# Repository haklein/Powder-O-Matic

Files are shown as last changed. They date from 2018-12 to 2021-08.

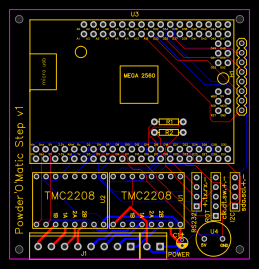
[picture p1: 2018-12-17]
schematics/PCB_Powder-O-Matic-Stepper-TMC2208-V1_20181217092319.png

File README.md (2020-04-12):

Powder'O'Matic Step Readme
==========================

## Overview

This Sketch controls two stepper motors via two TCM2208 stepper drivers. The drivers 
are controlled via dir/step pins and configured via Serial 2 and 3. Serial 1 is being
used to fetch values from a the scale. The target value is adjusted with a KY-040
rotary encoder. Dispensing can be started by pressing the push button of the rotary
encoder. A SSD1306 OLED display is used to display the current state, actual and target
value. The Kern scale needs to be configured for command mode ("rE Cr") with 19200 baud. 
The default values are set up for grain.
  
The KY-040 is evaluated by attaching a pin interrupt to the CLK signal (rotaryIsr())
The Stepper A is being turned via UART commands. Stepper B uses the AccelStep library.

Operation can be seen here: https://youtu.be/FhTphJCxM40 (prototype with a KERN PCB100-3)
and here: https://youtu.be/DZrE01YJ6Ys (final version in nice case with A&D FX120i balance)

The Autotrickler hardware (trickler and stepper motor adapter for the Lee Powder Thrower)
can be bought here: https://www.autotrickler.com

While Adam's Autotrickler hardware is the preferred option, you can find a motor adapter 
for the RCBS Powder Trickler #2 in the designs folder. A pulley for the RCBS pipe and a
case for the provided PCB layout can also be seen there. The case is ready-to-use for the
PCB, an SSD1309 1,54" OLED Display, the rotary, two subminiature switches (power and auto
mode), a DC socket and two G36 4-pin sockets for the stepper motors.

A complete BOM can be found here: https://github.com/haklein/Powder-O-Matic/blob/master/BOM.md

As I've been aksed multiple times, these config settings for the FX120i do work fine for me:

 btPr 2, bPs 5, Prt 3, Spd 20, trc 0, cond 0.

## Requirements

### Arduino libraries

- ArduinoMenu library
- TimerOne
- ClickEncoder - https://github.com/0xPIT/encoder
- Adafruit GFX Library
- TMC2208Stepper
- AccelStepper
- Adafruit SSD1306

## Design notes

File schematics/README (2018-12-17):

EasyEDA source (JSON file), PDF schematics, gerber file and PCB PNG.

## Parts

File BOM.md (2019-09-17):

Bill of Material
================

- P'o'M PCB (see schematics folder) or breadboard/prototype PCB
- RobotDyn Mega 2560 PRO (Embed) fitting the P'o'M PCB (or any other Mega 2560 based arduino if you do your own PCB)
- TMC2208 Board (I'm using the 1.0 from fysetc.com, make sure it's one where you can solder-bridge the NC pin to the
  serial input of the TMC (as that's used on the P'o'M PCB). You need one board for the trickler and one for the thrower.
- piezzo buzzer (U4) - I'm using a KEPO KPT-G1420A-K8437. It's a bit too big for the PCB but still connectable with a bit
  of tweaking
- capacitor (220 µF)
- resistors (R1 + R2) - 1k
- screw terminalls - Watch the spacing of the PCB, I'm using DECA MA212-350M02 
- pin headers and sockets
- RS232 ttl level converter, watch out, some of the ebay PCBs run insanely hot and don't work reliable (mostly SMD ones 
  without LED). The ones with MAX232 in DIP and LEDs worked fine for me
- KY040 rotary encoder
- SSD1306 display (resp. SSD1309 with 1.5" if you want to use the 3d printed case from the designs folder)
- two miniature switches for power switch and automatic mode switch
- DC socket
- GX16-4 plug and socket for the steppers
- 3d printed case from the designs folder (perfect fit for the P'o'M PCB)

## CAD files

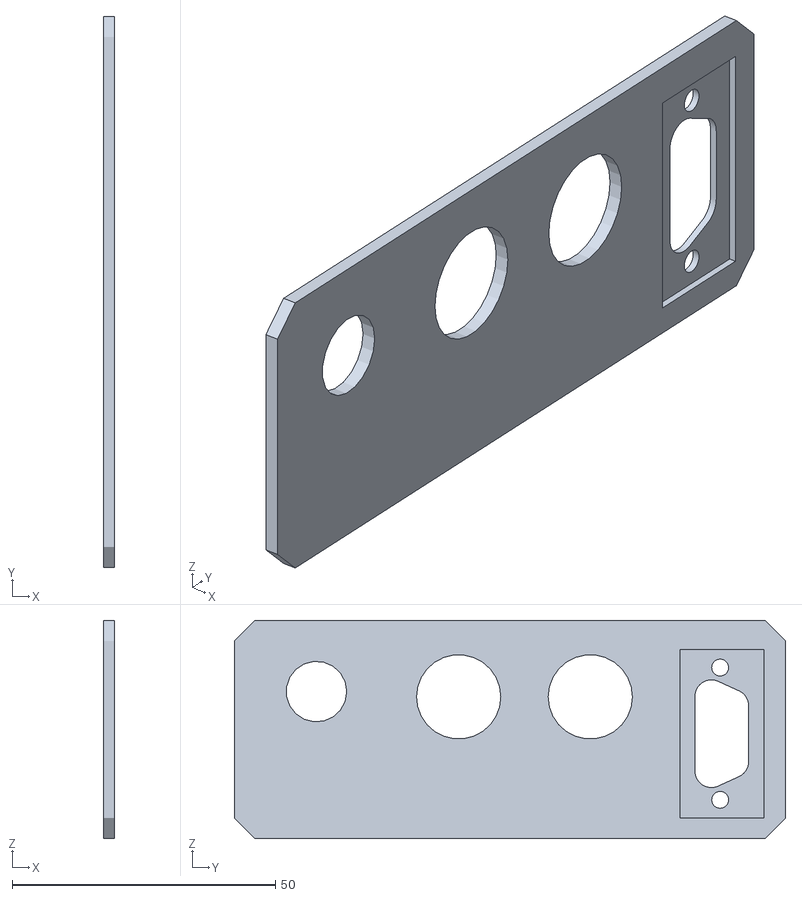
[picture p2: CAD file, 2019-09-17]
designs/pom_back_panel.stl
2.00 x 104.7 x 41.4

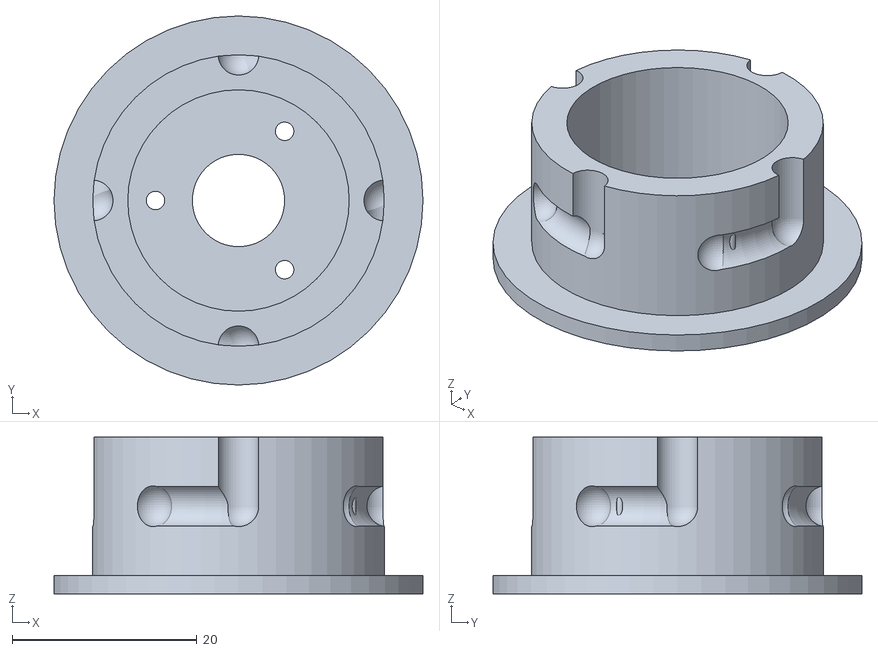
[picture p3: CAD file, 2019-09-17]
designs/straw-replacement_bottom.stl
40.0 x 40.0 x 17.0

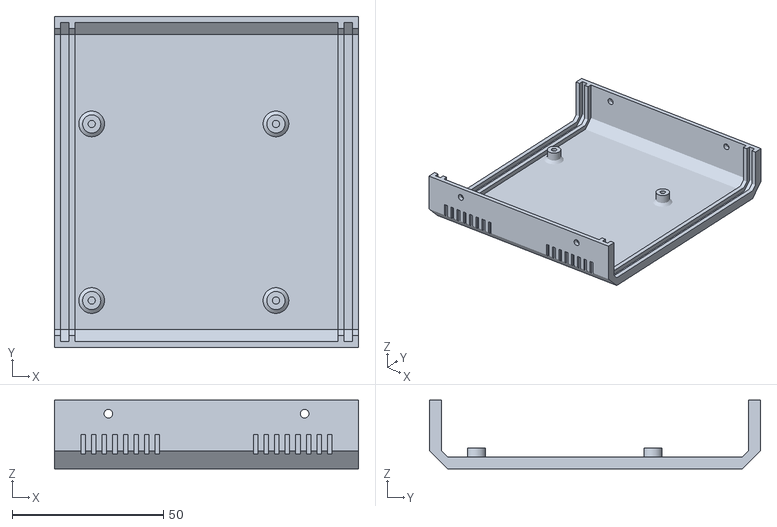
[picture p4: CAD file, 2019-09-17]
designs/pom_case_bottom.stl
100.6 x 109.5 x 22.8

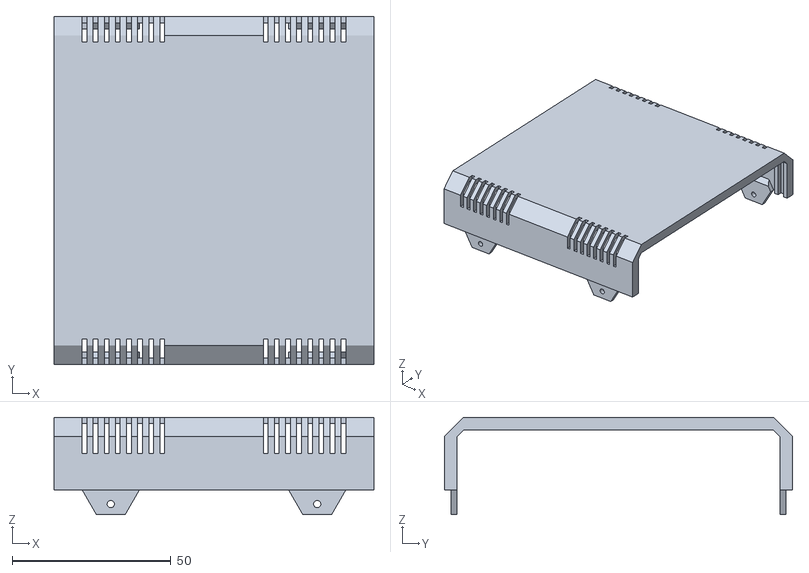
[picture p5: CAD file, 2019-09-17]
designs/pom_case_top.stl
100.6 x 109.5 x 30.6

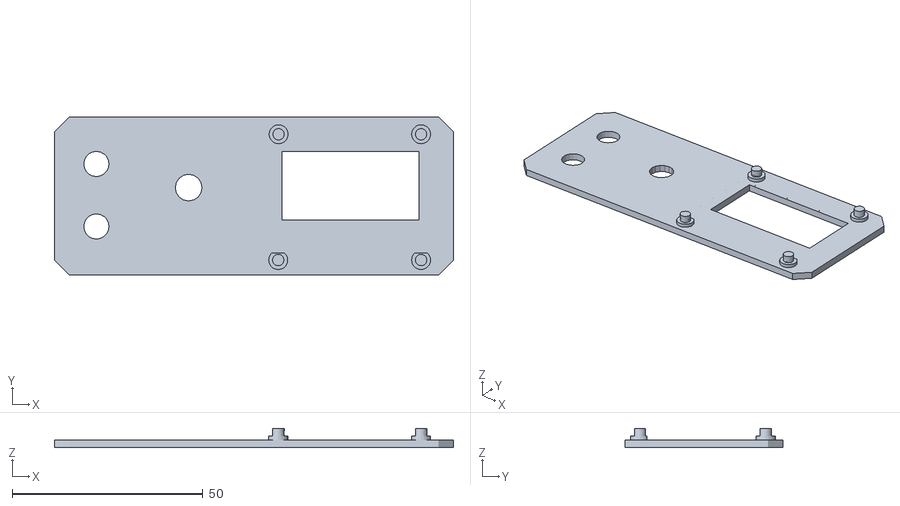
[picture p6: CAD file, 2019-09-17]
designs/pom_front_panel.stl
104.7 x 41.4 x 5.00

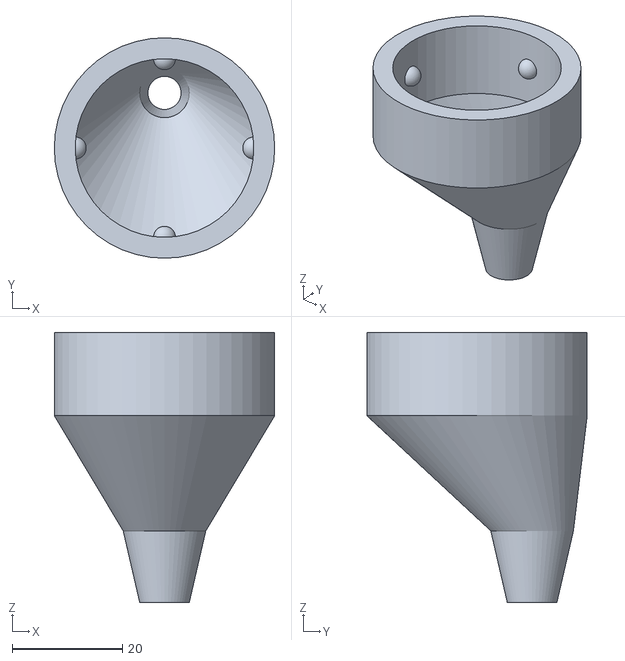
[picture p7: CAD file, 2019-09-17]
designs/straw-replacement_top.stl
40.0 x 40.0 x 49.0

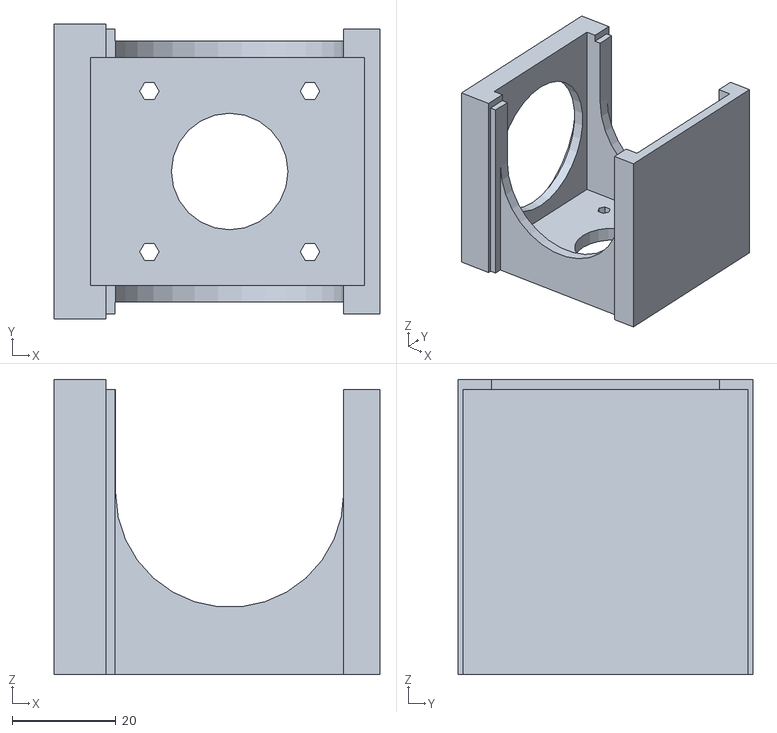
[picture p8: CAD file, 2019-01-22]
designs/RCBS_Trickler_NEMA17_mount.stl
62.9 x 57.0 x 57.0

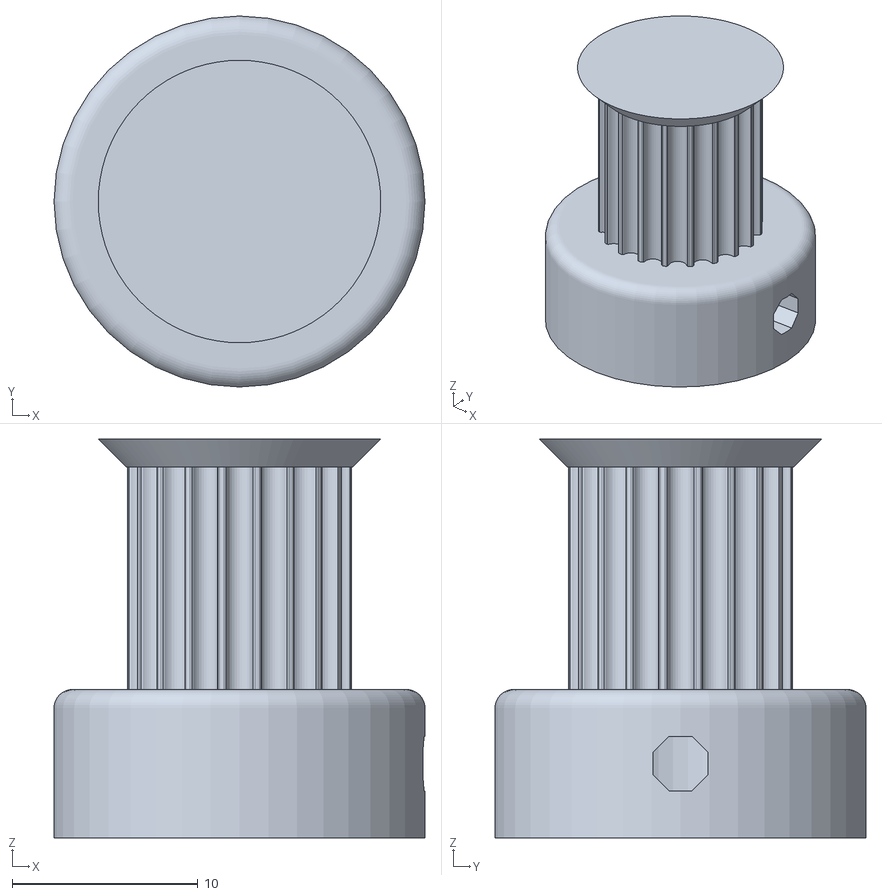
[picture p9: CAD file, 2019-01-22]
designs/RCBS_Trickler_shaft_pulley.stl
20.0 x 20.0 x 21.5

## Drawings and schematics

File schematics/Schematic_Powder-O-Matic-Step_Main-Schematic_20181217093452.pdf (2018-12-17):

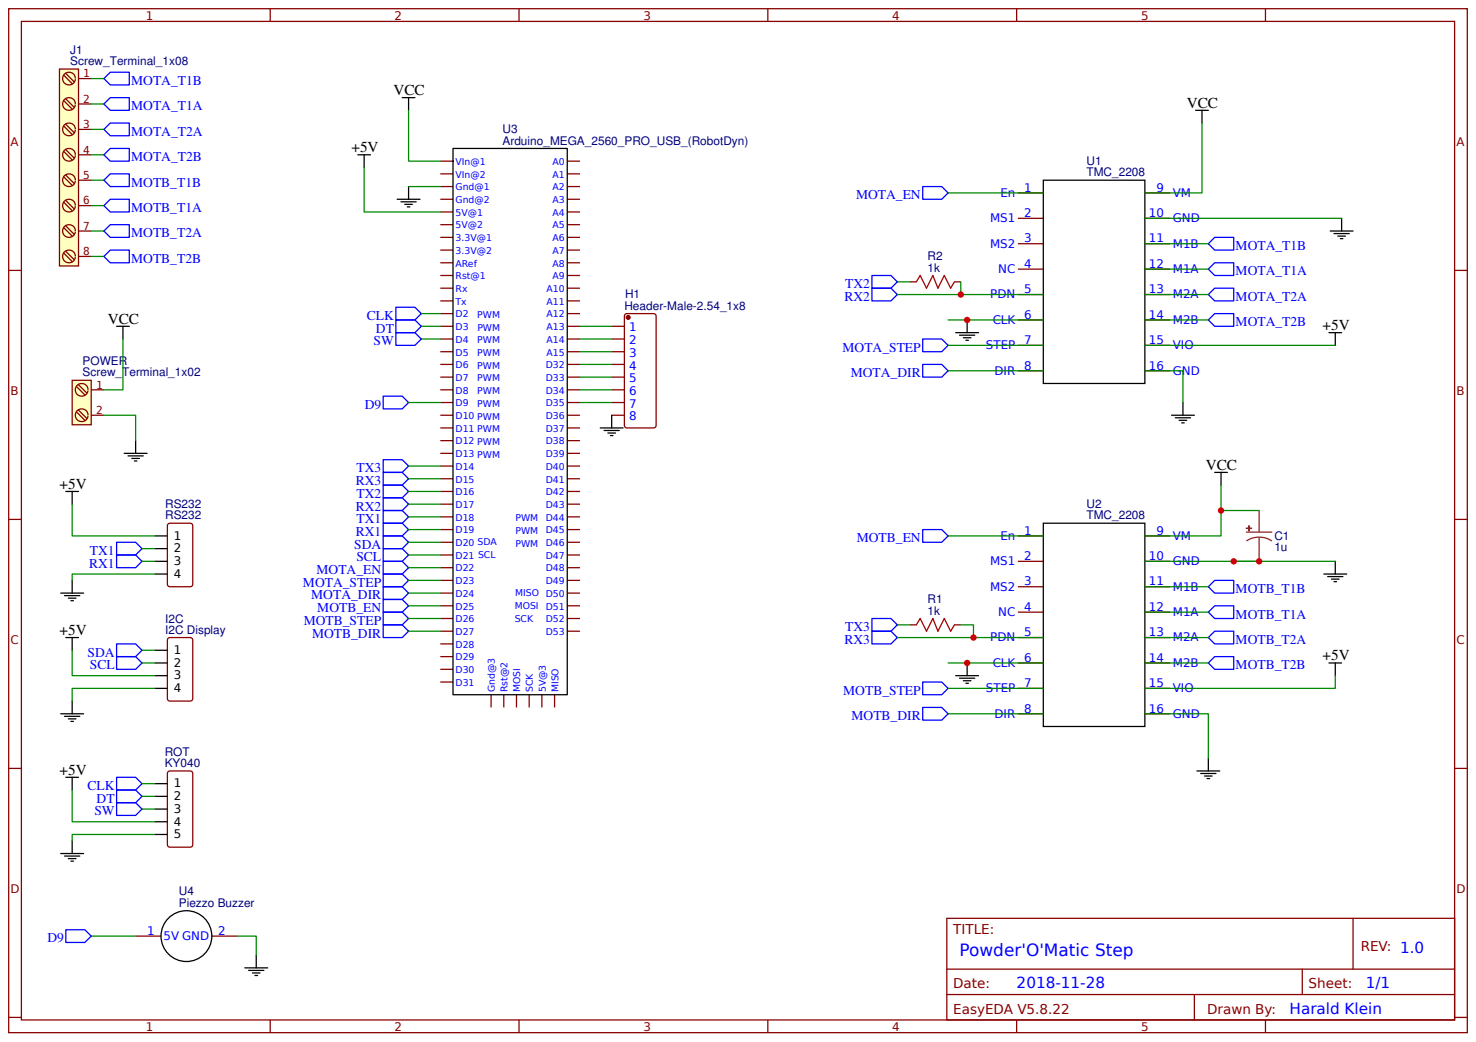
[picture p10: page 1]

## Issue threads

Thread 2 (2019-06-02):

Hilfe

Rajakob, 2019-06-02:
Guten Tag. Ich habe damit begonnen Ihr Projekt umzusetzen. Besten Dank vorweg eine wirklich tolle Lösung.  Ich verwende eine AnD FX120i jedoch scheitert die automatische Tarierung. Könne Sie mir bitte die Einstellungen mitteilen, welche Sie an der Waage gemacht haben damit die Waage von extern Tariert werden kann? Ebenfalls kann Ich nicht wie in Ihrem letzten Video die einzelnen Einstellungen z.B Trickler mA einstellen. Ist der Code noch Ihre „alte“ Version? Besten Dank für Ihre Hife. Freundliche Grüsse aus der Schweiz. Raoul Jakob
J.raoul@hotmail.com

haklein, 2021-08-25:
Die Einstellungen sollten jetzt wieder funktionieren. Die Einstellungen an der Waage kann ich derzeit nicht nachsehen, aber die optionen sind so weit schluessig im Handbuch erklaert.

Closed 2021-08-25.

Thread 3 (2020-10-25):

Display set-up menu

RowanNL, 2020-10-25:
Hello,

I've got the program and trickler working but i have a problem with entering the set-up menu.
When pressing the rotary encoder while start up it will enter set up but the whole screen just turns white.
I just used your program, I've tried both displays but the both do the same.

Can you help me out?

Thx!

I really love the powder-o-matic! It would be really nice to have the set up working as well.

RowanNL, 2020-12-12:
Gütentag, Wenn ich durch Drücken beim Start in das Setup-Menü gehen möchte, bleibt der Bildschirm weiß. Kannst du mir helfen? Es funktioniert auf deinem YouTube-Kanal...

danke im Voraus

RowanNL, 2021-01-13:
Hello Harald,

Could you help us?

regards,

RowanNL, 2021-01-13:
Hello Harald,

can you help us?

regards,

haklein, 2021-08-25:
I've found the reason for this issue with new arduino versions. Will be fixed in a few minutes.

Closed 2021-08-25.

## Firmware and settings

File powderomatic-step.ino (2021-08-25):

/*

     Powder'O'Matic Step

    Copyright (c) 2018 Harald Klein <hari@vt100.at>

    Licensed under GPL Version 3 - https://www.gnu.org/licenses/gpl-3.0.html

    This Sketch controls two stepper motors via two TCM2208 stepper drivers. The drivers
    are controlled via dir/step pins and configured via Serial 2 and 3. Serial 1 is being
    used to fetch values from a Kern PCB scale. The target value is adjusted with a KY-040
    rotary encoder. Dispensing can be started by pressing the push button of the rotary
    encoder. A SSD1306 OLED display is used to display the current state, actual and target
    value. The Kern scale needs to be configured for command mode ("rE Cr") with 19200 baud.
    The default values are set up for grain.

    The KY-040 is evaluated by attaching a pin interrupt to the CLK signal (rotaryIsr())
    The Stepper A is being turned via a timer interrupt (timer 5). Speed is adjusted by the
    microsteps() function of the TMC2208Stepper library.
*/

/*
  // gramm values
  #define MASSFILL_FAST_DELTA 0.05
  #define MASSFILL_SLOW_DELTA 0.02
  #define TRICKLE_DELTA 0.01
*/

// #define BALANCE_TYPE 1 // kern PCB 100-3
// #define BALANCE_TYPE 2 // A&D FX120i
// #define BALANCE_TYPE 3 // Sartorius
#define BALANCE_TYPE 2

// settings for Kern PCB
#if BALANCE_TYPE == 1
// grain values
#define MASSFILL_FAST_DELTA 1.4  // 1.2
#define MASSFILL_SLOW_DELTA 0.3
#define TRICKLE_DELTA 0.06
#define TRICKLE_DELAY 200

// settings for A&D FX120i
#elif BALANCE_TYPE == 2
#define MASSFILL_FAST_DELTA 0.8  // 1.2
#define MASSFILL_SLOW_DELTA 0.12
#define TRICKLE_DELTA 0.04
#define TRICKLE_DELAY 0

#endif


#define MOTA_SPEED_MAX 820 // 210000 / 256
#define MOTA_SPEED_MIN 59 // 15000 / 256

#define AUTOMODE_PIN 35 // set to 0 if no automode switch is connected

#define debug 20

// trickler stepper setup
#define MOTA_DIR 24
#define MOTA_STEP 23
#define MOTA_ENA 22
#define MOTA_MSTEPS 256 // 16
#define MOTA_SERIAL Serial2
#define MOTA_CURRENT_MA 500

// thrower stepper setup
#define MOTB_DIR 27
#define MOTB_STEP 26
#define MOTB_ENA 25
#define MOTB_MSTEPS 2
#define MOTB_SERIAL Serial3
#define MOTB_CURRENT_MA 300

#define THROWER_POSITION 170
#define THROWER_DELAY 300
#define THROWER_ENABLED true

#define BUZZER_PIN 9
#define BUZZER_SUCCESS_FREQ 2000
#define BUZZER_SUCCESS_DURATION 500
#define BUZZER_ERROR_FREQ 4000
#define BUZZER_ERROR_DURATION 300
#define BUZZER_ERROR_DELAY 300
#define BUZZER_ERROR_BEEP_COUNT 5

// baudrates
#define TMC2208_BAUDRATE 460800
#define KERN_PCB_BAUDRATE 19200

#define CONSOLE_BAUDRATE 115200

// mydisplay settings
#define OLED_RESET 34 // -1  Set to -1 for 0,96" SSD1306 display. 1.54" SSD1309 needs reset, pin 34 is recommended
#define SCREEN_WIDTH 128 // OLED display width, in pixels
#define SCREEN_HEIGHT 64 // OLED display height, in pixels
#define OLED_I2C_ADDRESS 0x3D // 0x3c 0.96" 

#define fontX 5
#define fontY 9
#define MAX_DEPTH 3
/// #define textScale 1

// rotary encoder settings
#define K040_SW 4  // D22, pin 74
#define K040_DT 3 // D24, pin 72
#define K040_CLK 2   //  int pin  alt: // D26, pin 70

#define ROTARY_DELTA_VALUE -0.1  // change sign to adjust for rotary direction
#define ROTARY_DEBOUNCE_MILLIS 5

#define CONFIG_MAGIC 0xdeadbeef
#define CONFIG_MIN_VER 1
#define CONFIG_VER 1

// config section end

#include <EEPROM.h>
#include <Arduino.h>  // for type definitions

#include <menu.h>
#include <TimerOne.h>

#include <ClickEncoder.h>
#include <menuIO/clickEncoderIn.h>
#include <menuIO/keyIn.h>
#include <menuIO/chainStream.h>
#include <menuIO/serialOut.h>
#include <menuIO/adafruitGfxOut.h>
#include <menuIO/serialIn.h>

#include <TMC2208Stepper.h>
#include <AccelStepper.h>

#include <SPI.h>
#include <Wire.h>
#include <Adafruit_GFX.h>
#include <Adafruit_SSD1306.h>

template <class T> int EEPROM_writeAnything(int ee, const T& value)
{
  const byte* p = (const byte*)(const void*)&value;
  unsigned int i;
  for (i = 0; i < sizeof(value); i++)
    EEPROM.write(ee++, *p++);
  return i;
}

template <class T> int EEPROM_readAnything(int ee, T& value)
{
  byte* p = (byte*)(void*)&value;
  unsigned int i;
  for (i = 0; i < sizeof(value); i++)
    *p++ = EEPROM.read(ee++);
  return i;
}

struct config_t {
  long int magic = CONFIG_MAGIC;
  int confVer = CONFIG_VER;
  int balanceType = BALANCE_TYPE;
  int motaCurrent = MOTA_CURRENT_MA;
  int motaSpeedMax = MOTA_SPEED_MAX;
  int motaSpeedMin = MOTA_SPEED_MIN;
  int motaMsteps = MOTA_MSTEPS;
  int motbCurrent = MOTB_CURRENT_MA;
  int motbMsteps = MOTB_MSTEPS;
  bool throwerEnabled = THROWER_ENABLED;
  int throwerDelay = THROWER_DELAY;
  int throwerPosition = THROWER_POSITION;
  float massfillFastDelta = MASSFILL_FAST_DELTA;
  float massfillSlowDelta = MASSFILL_SLOW_DELTA;
  float trickleDelta = TRICKLE_DELTA;
  int trickleDelay = TRICKLE_DELAY;
} configData;

ClickEncoder clickEncoder(K040_CLK, K040_DT, K040_SW, 4); // last parameter: steps per notch
ClickEncoderStream encStream(clickEncoder, 1);

TMC2208Stepper driverA = TMC2208Stepper(&MOTA_SERIAL);
TMC2208Stepper driverB = TMC2208Stepper(&MOTB_SERIAL);

AccelStepper stepperB(AccelStepper::DRIVER, MOTB_STEP, MOTB_DIR);

Adafruit_SSD1306 myDisplay(SCREEN_WIDTH, SCREEN_HEIGHT, &Wire, OLED_RESET);

volatile float targetValue = 5;
bool automaticModeEnabled = false; //AUTOMODE_PIN != 0 ? true : false;

void rotaryISR() {
  static unsigned long lastInterruptTime = 0;
  unsigned long interruptTime = millis();
  unsigned long delta = millis() - lastInterruptTime;
  int multi = sq(500 - min(delta, 500)) / 25000 + 1;

  // debounce 5ms
  if (delta > ROTARY_DEBOUNCE_MILLIS) {

    if (digitalRead(K040_DT) == LOW)
    {
      targetValue = targetValue - ROTARY_DELTA_VALUE * multi;
    }
    else {

      targetValue = targetValue + ROTARY_DELTA_VALUE * multi;
    }
    lastInterruptTime = interruptTime;
  }
}

void timerIsr() {
  clickEncoder.service();
}


const colorDef<uint16_t> colors[6] MEMMODE = {
  {{BLACK, WHITE}, {BLACK, WHITE, WHITE}}, //bgColor
  {{WHITE, BLACK}, {WHITE, BLACK, BLACK}}, //fgColor
  {{WHITE, BLACK}, {WHITE, BLACK, BLACK}}, //valColor
  {{WHITE, BLACK}, {WHITE, BLACK, BLACK}}, //unitColor
  {{WHITE, BLACK}, {BLACK, BLACK, BLACK}}, //cursorColor
  {{BLACK, WHITE}, {WHITE, BLACK, BLACK}}, //titleColor
};

/*
  const colorDef<uint16_t> colors[] MEMMODE = {
  {{WHITE, BLACK}, {WHITE, BLACK, BLACK}}, //bgColor
  {{BLACK, WHITE}, {BLACK, WHITE, WHITE}}, //fgColor
  {{BLACK, WHITE}, {BLACK, WHITE, WHITE}}, //valColor
  {{BLACK, WHITE}, {BLACK, WHITE, WHITE}}, //unitColor
  {{BLACK, WHITE}, {WHITE, WHITE, WHITE}}, //cursorColor
  {{BLACK, WHITE}, {WHITE, BLACK, BLACK}}, //titleColor
  };
*/

result showEvent(eventMask e, navNode& nav, prompt& item) {
  Serial.print(F("event:"));
  Serial.print(e);
  return proceed;
}

result alert(menuOut& o, idleEvent e);
result doAlert(eventMask e, prompt &item);

CHOOSE(configData.balanceType, scaleMenu, "Scale", doNothing, noEvent, noStyle
       , VALUE("Kern PCB 100-3", 1, doNothing, noEvent)
       , VALUE("A&D FX120i", 2, doNothing, noEvent)
       , VALUE("Sartorius", 3, doNothing, noEvent)
      );

SELECT(configData.motaMsteps, motamstepMenu, "Trickler MSteps", doNothing, noEvent, noStyle
       , VALUE("1", 1, doNothing, noEvent)
       , VALUE("2", 2, doNothing, noEvent)
       , VALUE("4", 4, doNothing, noEvent)
       , VALUE("8", 8, doNothing, noEvent)
       , VALUE("16", 16, doNothing, noEvent)
       , VALUE("32", 32, doNothing, noEvent)
       , VALUE("64", 64, doNothing, noEvent)
       , VALUE("128", 128, doNothing, noEvent)
       , VALUE("256", 256, doNothing, noEvent)
      );

SELECT(configData.motbMsteps, motbmstepMenu, "Thrower MSteps", doNothing, noEvent, noStyle
       , VALUE("1", 1, doNothing, noEvent)
       , VALUE("2", 2, doNothing, noEvent)
       , VALUE("4", 4, doNothing, noEvent)
       , VALUE("8", 8, doNothing, noEvent)
       , VALUE("16", 16, doNothing, noEvent)
       , VALUE("32", 32, doNothing, noEvent)
       , VALUE("64", 64, doNothing, noEvent)
       , VALUE("128", 128, doNothing, noEvent)
       , VALUE("256", 256, doNothing, noEvent)
      );

SELECT(configData.throwerEnabled, throwenaMenu, "Thr. Enabled", doNothing, noEvent, noStyle
       , VALUE("Yes", true, doNothing, noEvent)
       , VALUE("No", false, doNothing, noEvent)
      );

MENU(mainMenu, "Powder'O'Matic Setup", doNothing, noEvent, wrapStyle
     , SUBMENU(scaleMenu)
     //     , FIELD(test, "Test", "%", 0, 100, 10, 1, doNothing, noEvent, wrapStyle)
     , FIELD(configData.motaCurrent, "Trickler Cur", "mA", 100, 2000, 100, 10, doNothing, noEvent, noStyle)
     , SUBMENU(motamstepMenu)
     , FIELD(configData.motaSpeedMin, "Tr MinSpd", "", 10, 300, 10, 1, doNothing, noEvent, noStyle)
     , FIELD(configData.motaSpeedMax, "Tr MaxSpd", "", 100, 1500, 100, 10, doNothing, noEvent, noStyle)
     , SUBMENU(throwenaMenu)
     , FIELD(configData.motbCurrent, "Thrower Curr", "mA", 100, 2000, 100, 10, doNothing, noEvent, noStyle)
     , SUBMENU(motbmstepMenu)
     , FIELD(configData.throwerDelay, "Thrower Delay", "ms", 0, 1000, 100, 10, doNothing, noEvent, noStyle)
     , FIELD(configData.throwerPosition, "Thrower Pos", "step", 0, 1000, 100, 10, doNothing, noEvent, noStyle)
     , FIELD(configData.massfillFastDelta, "Fast Delta", "gr", 0.0, 5, 1, 0.1, doNothing, noEvent, noStyle)
     , FIELD(configData.massfillSlowDelta, "Slow Delta", "gr", 0.0, 2, 0.1, 0.01, doNothing, noEvent, noStyle)
     , FIELD(configData.trickleDelta, "Trickle Delta", "gr", 0.0, 0.2, 0.1, 0.01, doNothing, noEvent, noStyle)
     , FIELD(configData.trickleDelay, "Trickle Delay", "ms", 0, 1000, 100, 10, doNothing, noEvent, noStyle)
     , OP("<Save", writeEprom, enterEvent)
     , OP("<Factory defaults", resetEprom, enterEvent)
     //     , EXIT("<Back")
    );


MENU_INPUTS(in, &encStream);

MENU_OUTPUTS(out, MAX_DEPTH
             , ADAGFX_OUT(myDisplay, colors, fontX, fontY, {0, 0, SCREEN_WIDTH / fontX, SCREEN_HEIGHT / fontY})
             , NONE // needs to have two items
            );

NAVROOT(nav, mainMenu, MAX_DEPTH, in, out);

bool writeEprom() {
  Serial.println("Writing EEPROM Config data");
  EEPROM_writeAnything(0, configData);
  return true;
}

bool resetEprom() {
  config_t factoryConfigData;
  EEPROM_writeAnything(0, factoryConfigData);
  return true;
}

void configMenu() {


  myDisplay.clearDisplay();
  myDisplay.setTextSize(1);
  myDisplay.setCursor(0, 0);
  myDisplay.setTextColor(BLACK, WHITE); // 'inverted' text
  myDisplay.println("Powder'O'Matic Stp v1");
  myDisplay.setCursor(0, 14);
  myDisplay.setTextColor(WHITE);
  myDisplay.setTextSize(2);
  myDisplay.println("Setup..");

  myDisplay.display();
  myDisplay.setTextSize(1);

  while (digitalRead(K040_SW) == LOW); // wait until button is released to not feed input into nav.doInput()
  // delay(2000);

  while (true) {

    nav.doInput();
    if (nav.changed(0)) {//only draw if changed
      nav.doOutput();
      myDisplay.display();
    }
  }
}
void setup() {
  Serial.begin(CONSOLE_BAUDRATE);
  Serial1.begin(KERN_PCB_BAUDRATE);
  Serial2.begin(TMC2208_BAUDRATE);
  Serial3.begin(TMC2208_BAUDRATE);

  Serial.println("reading EEPROM config data");
  EEPROM_readAnything(0, configData);
  if ((configData.magic != CONFIG_MAGIC) || (configData.confVer < CONFIG_MIN_VER)) {
    Serial.println("ERROR, invalid EEPROM config data, writing default config");
    config_t newConfigData;
    EEPROM_writeAnything(0, newConfigData);
    configData = newConfigData;
    Serial.print("initialized EEPROM config data to default values, version: ");
    Serial.println(configData.confVer);
    delay(100);

  } else {
    Serial.print("EEPROM config valid, version: ");
    Serial.println(configData.confVer);
  }


  Serial.println("Powder'O'Matic Step startup...");
  if (!myDisplay.begin(SSD1306_SWITCHCAPVCC, OLED_I2C_ADDRESS)) { // Address 0x3C
    Serial.println("SSD1306 allocation failed");
  }

  myDisplay.clearDisplay();
  myDisplay.setTextSize(1);
  myDisplay.setCursor(0, 0);
  myDisplay.setTextColor(BLACK, WHITE); // 'inverted' text
  myDisplay.println("Powder'O'Matic Stp v1");
  myDisplay.setCursor(0, 14);
  myDisplay.setTextColor(WHITE);
  myDisplay.setTextSize(2);
  myDisplay.println("Start..");

  myDisplay.display();

  pinMode(K040_DT, INPUT_PULLUP);
  pinMode(K040_SW, INPUT_PULLUP);
  pinMode(K040_CLK, INPUT_PULLUP);

  if (AUTOMODE_PIN != 0) pinMode(AUTOMODE_PIN, INPUT_PULLUP);

  // attachInterrupt(digitalPinToInterrupt(K040_CLK), rotaryISR, LOW);

  driverA.push();
  driverB.push();                // Reset registers

  // Prepare pins
  pinMode(MOTA_ENA, OUTPUT);
  pinMode(MOTB_ENA, OUTPUT);

  pinMode(MOTA_STEP, OUTPUT);
  pinMode(MOTA_DIR, OUTPUT);

  pinMode(MOTB_STEP, OUTPUT);
  pinMode(MOTB_DIR, OUTPUT);

  if (BUZZER_PIN)
    pinMode(BUZZER_PIN, OUTPUT);

  digitalWrite(MOTA_ENA, HIGH);   // Disable driver in hardware
  digitalWrite(MOTB_ENA, HIGH);

  driverA.pdn_disable(true);     // Use PDN/UART pin for communication
  driverA.I_scale_analog(true); // Use internal voltage reference
  driverA.rms_current(configData.motaCurrent);      // Set driver current 500mA
  // driverB.en_spreadCycle(1);
  driverA.toff(2);               // Enable driver in software
  driverA.mstep_reg_select(true); // ignore MS1 + MS2
  driverA.microsteps(configData.motaMsteps);
  driverA.ihold(0);
  digitalWrite(MOTA_DIR, LOW);

  driverB.pdn_disable(true);     // Use PDN/UART pin for communication
  driverB.I_scale_analog(true); // Use internal voltage reference
  driverB.rms_current(configData.motbCurrent);      // Set driver current 500mA
  // driverB.en_spreadCycle(1);
  driverB.toff(2);               // Enable driver in software
  driverB.mstep_reg_select(true); // ignore MS1 + MS2
  driverB.microsteps(configData.motbMsteps);
  driverB.ihold(0);


  digitalWrite(MOTA_ENA, LOW);
  digitalWrite(MOTB_ENA, LOW);    // Enable driver in hardware

  if (debug > 9) {
    uint32_t data = 0;
    Serial.print("Mot A DRV_STATUS = 0x");
    driverA.DRV_STATUS(&data);
    Serial.println(data, HEX);
    data = 0;
    Serial.print("Mot B DRV_STATUS = 0x");
    driverB.DRV_STATUS(&data);
    Serial.println(data, HEX);
  }

  stepperB.setMaxSpeed(20000000);
  stepperB.setAcceleration(5000);


  Timer1.initialize(1000);
  Timer1.attachInterrupt(timerIsr);
  // setup end

  if (digitalRead(K040_SW) == LOW) {
    Serial.println("Setup mode");
    configMenu();
  }

  clickEncoder.setAccelerationEnabled(true);
}

void throwPowder() {
  if (configData.throwerEnabled) {
    stepperB.moveTo(configData.throwerPosition * configData.motbMsteps);
    stepperB.runToPosition();
    delay(configData.throwerDelay);
    stepperB.moveTo(0 * configData.motbMsteps);
    stepperB.runToPosition();
  }
}

// derive motor speed from value
uint32_t speedFromValue(float currentValue, float targetValue) {
  float delta = targetValue - currentValue;
  if (delta > configData.massfillFastDelta) {
    Serial.print("MAX Speed: ");
    Serial.println((uint32_t) configData.motaSpeedMax * configData.motaMsteps);
    return (uint32_t) configData.motaSpeedMax * configData.motaMsteps;
  }
  if (delta < configData.massfillSlowDelta) {
    Serial.println("MIN Speed");
    return configData.motaSpeedMin * configData.motaMsteps;
  }
  uint32_t newSpeed = map(delta * 10, configData.massfillSlowDelta * 10,
                          configData.massfillFastDelta * 10, configData.motaSpeedMin, configData.motaSpeedMax);
  Serial.print("Speed: ");
  Serial.println(newSpeed * configData.motaMsteps);
  return newSpeed * configData.motaMsteps;
}
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
void loop() {

  targetValue += clickEncoder.getValue() / 10.0;

  if (currentState != lastState) {
    Serial.print("State change: ");
    Serial.println(stateToString(currentState));
    lastState = currentState;
  }
  switch (currentState) {
    case IDLE:
      readScaleStableOrUnstable(&value);
      if (AUTOMODE_PIN != 0)
        automaticModeEnabled = (digitalRead(AUTOMODE_PIN) == LOW) ? true : false;
      if ((digitalRead(K040_SW) == LOW) || (automaticModeEnabled && (value < 0.1 && value > -0.1)) ) {
        currentState = WAIT_FOR_TARE;
        updateDisplay();
        taraScale();
      }

      break;
    case WAIT_FOR_TARE:
      while (readScaleStable(&value) != 1)
        updateDisplay();
      if (value == 0.0) {
        startTimestamp = millis();
        currentState = MASSFILL_FAST;
        updateDisplay();
        driverA.VACTUAL(speedFromValue(value, targetValue));
        if (configData.throwerEnabled) throwPowder();
      }
      break;
    case MASSFILL_FAST:
      if (readScaleStableOrUnstable(&value) != -1) {
        /*
                Serial.print("Value: ");
                Serial.println(value);
        */
        if (value > targetValue - configData.massfillFastDelta) {
          currentState = MASSFILL_SLOW;
          driverA.VACTUAL(speedFromValue(value, targetValue));
        }
      }
      break;
    case MASSFILL_SLOW:
      if (readScaleStableOrUnstable(&value) != -1) {
        driverA.VACTUAL(speedFromValue(value, targetValue));
        if (value > targetValue - configData.massfillSlowDelta) {
          currentState = TRICKLE;
          if (configData.balanceType == 1) // give the kern pcb some time to get stable in next state
            driverA.VACTUAL((uint32_t) 0);
        }
      }
      break;
    case TRICKLE:
      if (configData.balanceType == 1) {
        if (readScaleStableOrUnstable(&value) == 1) {
          if (value > targetValue - configData.trickleDelta) {
            currentState = FINISHED;
            driverA.VACTUAL((uint32_t) 0);
          } else {
            Serial.println("trickling..");
            driverA.VACTUAL(speedFromValue(value, targetValue));
          }
        } else {
          Serial.println("no stable");
          driverA.VACTUAL((uint32_t) 0);
          delay(configData.trickleDelay);
        }
      } else {
        // A&D FX120i
        readScaleStableOrUnstable(&value);
        if (value > targetValue - configData.trickleDelta) {
          currentState = FINISHED;
          driverA.VACTUAL((uint32_t) 0);

        }

      }
      break;
    case FINISHED:
      //Serial.println("STATE:FINISHED");
      driverA.VACTUAL((uint32_t) 0);
      Serial.print("Total time: ");
      Serial.println((millis() - startTimestamp) / 1000);
      delay(500);;
      while (readScaleStableOrUnstable(&value) != 1);
      if (abs(value  - targetValue) < configData.trickleDelta) {
        // success
#ifdef BUZZER_PIN
        tone(BUZZER_PIN, BUZZER_SUCCESS_FREQ, BUZZER_SUCCESS_DURATION);
#endif
        currentState = IDLE;
      } else {
        currentState = ERROR;
        updateDisplay();

      }
      break;
    case ERROR:
      //Serial.println("STATE:ERROR");
      driverA.VACTUAL((uint32_t) 0);
      for (int i = 0; i < BUZZER_ERROR_BEEP_COUNT; i++) {
#ifdef BUZZER_PIN
        tone(BUZZER_PIN, BUZZER_ERROR_FREQ, BUZZER_ERROR_DURATION);
#endif
        delay(BUZZER_ERROR_DELAY);
      }
      currentState = IDLE;
      break;
    default:
      break;
  }

  updateDisplay();
}

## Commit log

2018-12-07 add defines for values, use UART stepper control instead of timer interrupt for motor A
2018-12-07 remove remainders from timer based stepping
2018-12-17 display automode, improve display updates, go from error to idle without keypress
    [powderomatic-step.ino]
2018-12-17 add schematics
2018-12-21 add A&D FX120i support, change pin definitions to match the v1 PCB, use internal pullups for the rotary pins
2019-01-22 automode switch, LCD reset
    [powderomatic-step.ino]
2019-01-22 add RCBS Trickler NEMA17 mount STL files
    [RCBS_Trickler_NEMA17_mount.stl, RCBS_Trickler_shaft_pulley.stl]
2019-04-05 a straw replacement for Adam's Autothrower (Autotrickler)
    [straw-replacement_bottom.stl, straw-replacement_top.stl]
2019-05-17 Add 3d printer designs for case
    [pom_back_panel.stl, pom_case_bottom.stl, pom_case_top.stl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]
2020-04-12 fix error: variable "colors" with dynamic initialization put into program memory area
    [powderomatic-step.ino]
2021-08-25 fixes #3 - white setup screen
    removing the PROGMEM in the earlier 'fix' was the wrong approach. To avoid the compiler error, the number of lines needs to be specified for the colors[] array. This has just been tested and fixes #3 - white setup screen.
    [powderomatic-step.ino]
